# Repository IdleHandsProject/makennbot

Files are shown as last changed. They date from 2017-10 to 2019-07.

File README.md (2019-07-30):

# Make: Arduino Neural Network Robot
A light avoiding robot that navigates using a Neural Network.

# Watch the Build Series!
3 Part Series on YouTube (https://youtu.be/wtNaPLmpy1I)

BOM Here: https://www.findchips.com/org/10-open-hardware/list/53285-makennbot

HackADay.io Link: https://hackaday.io/project/27938-arduino-neural-network-robot

Motors: https://www.pololu.com/product/2357

OLED: https://www.aliexpress.com/item/White-0-66-inch-OLED-Display-Module-64x48-0-66-LCD-Screen-SPI-for-Arduino-AVR/32782787258.html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

Battery(anything with JST SH connector): https://www.sparkfun.com/products/13851

A viewer created a method to train the network using a Python Script, Check it out here: https://github.com/JonComo/Arduino_weight_trainer

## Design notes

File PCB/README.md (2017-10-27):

# Make: Arduino Neural Network Robot
A light avoiding robot that navigates using a Neural Network.

BOM Here: https://www.findchips.com/org/10-open-hardware/list/53285-makennbot

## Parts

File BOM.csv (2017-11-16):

ref | value | footprint | Digikey Part No. | Mouser Part No. | Quantity
U4 | MCP73831T | idlehands_footprints:sot23-5 | MCP73831T-2ACI/OTCT-ND |  | 1
U5 | DRV8835 | project_footprints:WSON-12-2x3 | 296-30391-1-ND |  | 1
U3 | AP2112K-3.3V | TO_SOT_Packages_SMD:SOT-23-5 | AP2112K-3.3TRG1DICT-ND |  | 1
Y1 | Crystal_Small | project_footprints:crystal_smd_5x3.2mm | 535-9536-1-ND |  | 1
R18 | 33k | Resistors_SMD:R_0603 | 311-33KGRCT-ND |  | 1
P3 | CONN_01X07 | Pin_Headers:Pin_Header_Straight_1x07 | S7040-ND |  | 1
D1 | D_Schottky | idlehands_footprints:sod80c | B130-FDICT-ND |  | 1
R2 | 330 | Resistors_SMD:R_0603 | 311-330GRCT-ND |  | 1
C13 | 10uF | Capacitors_SMD:C_0603 | 587-1256-1-ND |  | 1
F1 | 500mA | project_footprints:c_1206 | 507-1803-1-ND |  | 1
R4 R5 | 47K | Resistors_SMD:R_0603 | 311-47.0KHRCT-ND |  | 2
C6 C9 | 2.2uF | Capacitors_SMD:C_0603 | 587-1430-1-ND |  | 2
C3 C5 C1 C11 C12 C14 C15 | 0.1uF | Capacitors_SMD:C_0603 | 478-1239-1-ND |  | 7
C10 C7 | 4.7uF | Capacitors_SMD:C_0603 | 490-5421-1-ND |  | 2
D6 | RX | project_footprints:Led_0603 | 160-1447-1-ND |  | 1
U1 | 74AHC1G125 | project_footprints:sot23-5 | 1727-6024-1-ND |  | 1
R1 | 100k | Resistors_SMD:R_0603 | 311-100KHRCT-ND |  | 1
D7 | TX | project_footprints:Led_0603 | 160-1448-1-ND |  | 1
P17 | DBG_CONN | Pin_Headers:Pin_Header_Straight_2x05_Pitch1.27mm | 1175-1627-ND |  | 1
P4 P5 | MOTOR_A | Capacitors_SMD:C_1206 | F3781-ND |  | 2
PH4 PH3 PH2 PH1 | Photores | Pin_Headers:Pin_Header_Straight_1x02 | PDV-P8001-ND |  | 4
Q1 | Q_PMOS_DSG | project_footprints:SOT23 | DMG2307L-7DICT-ND |  | 1
C2 C4 | 15pF | Capacitors_SMD:C_0603 | 1276-2192-1-ND |  | 2
Q2 | Q_PMOS_GSD | idlehands_footprints:SOT23 | IRLML6402PBFCT-ND |  | 1
U2 | SAMD21G18 | project_footprints:TQFP-48_7x7mm_Pitch0.5mm | ATSAMD21G18A-AU-ND |  | 1
P1 | USB_OTG | Connect:USB_Micro-B | 609-4618-1-ND |  | 1
P2 | BatteryHolder | Connectors_JST_PH:Connectors_JST_S2B-PH-K | 36-2479-ND |  | 1
R14 R13 R19 | 1k | Resistors_SMD:R_0603 | 311-1.0KGRCT-ND |  | 3
SW2 SW3 SW4 | SW_PUSH | Buttons_Switches_SMD:SW_SPST_EVQPE1 | 401-1702-1-ND |  | 3
L1 | FB - 30Ohm | project_footprints:R_SM0603 | 445-2986-1-ND |  | 1
R3 R6 R9 R11 R15 | 10k | Resistors_SMD:R_0603 | 311-10KGRCT-ND |  | 5
C8 | 1uF | Capacitors_SMD:C_0603 | 1276-1946-1-ND |  | 1

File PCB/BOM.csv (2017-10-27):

ref | value | footprint | Digikey Part No. | Mouser Part No. | Quantity
C14 C15 | 0.1uF | Capacitors_SMD:C_0603 | 490-6328-1-ND |  | 2
C3 C5 C1 C11 C12 | 0.1uF | Capacitors_SMD:C_0603 | 311-1343-1-ND |  | 5
U4 | MCP73831T | idlehands_footprints:sot23-5 | MCP73831T-2ACI/OTCT-ND |  | 1
U5 | DRV8835 | project_footprints:WSON-12-2x3 | 296-30391-1-ND |  | 1
U3 | AP2112K-3.3V | TO_SOT_Packages_SMD:SOT-23-5 | AP2112K-3.3TRG1DICT-ND |  | 1
D1 | D_Schottky | idlehands_footprints:sod80c | B130-FDICT-ND |  | 1
R3 R6 R9 R11 R15 | 10k | Resistors_SMD:R_0603 | 311-10KJRCT-ND |  | 5
F1 | 500mA | project_footprints:c_1206 | 507-1803-1-ND |  | 1
C2 C4 | 15pF | Capacitors_SMD:C_0603 | 712-1261-1-ND |  | 2
R18 | 33k | Resistors_SMD:R_0603 | 311-33KJRCT-ND |  | 1
SW2 | SW_PUSH | Buttons_Switches_SMD:SW_SPST_EVQPE1 | CKN9112CT-ND |  | 1
Y1 | Crystal_Small | project_footprints:crystal_smd_5x3.2mm | 631-1002-1-ND |  | 1
SW3 | SW_PUSH | Buttons_Switches_SMD:SW_SPST_EVQPE1 | CKN9084CT-ND |  | 1
D6 | RX | project_footprints:Led_0603 | 160-1447-1-ND |  | 1
R2 | 330 | Resistors_SMD:R_0603 | 311-330JRCT-ND |  | 1
C13 | 10uF | Capacitors_SMD:C_0603 | 311-1729-1-ND |  | 1
U1 | 74AHC1G125 | project_footprints:sot23-5 | 1727-6024-1-ND |  | 1
P1 | USB_OTG | Connect:USB_Micro-B | 609-4618-1-ND |  | 1
C9 | 2.2uF | Capacitors_SMD:C_0603 | 490-10451-1-ND |  | 1
R1 | 100k | Resistors_SMD:R_0603 | 311-100KLRCT-ND |  | 1
D7 | TX | project_footprints:Led_0603 | 160-1448-1-ND |  | 1
P17 | DBG_CONN | Pin_Headers:Pin_Header_Straight_2x05_Pitch1.27mm | 1175-1627-ND |  | 1
P4 P5 | MOTOR_A | Capacitors_SMD:C_1206 | F3781-ND |  | 2
C10 C7 | 4.7uF | Capacitors_SMD:C_0603 | 490-5915-1-ND |  | 2
PH4 PH3 PH2 PH1 | Photores | Pin_Headers:Pin_Header_Straight_1x02 | PDV-P8001-ND |  | 4
Q1 | Q_PMOS_DSG | project_footprints:SOT23 | DMG2307L-7DICT-ND |  | 1
C6 | 2.2uF | Capacitors_SMD:C_0603 | 1276-1291-1-ND |  | 1
R4 R5 | 47K | Resistors_SMD:R_0603 | 311-47.0KLRCT-ND |  | 2
R14 R13 R19 | 1k | Resistors_SMD:R_0603 | 311-1.0KJRCT-ND |  | 3
Q2 | Q_PMOS_GSD | idlehands_footprints:SOT23 | IRLML6402PBFCT-ND |  | 1
U2 | SAMD21G18 | project_footprints:TQFP-48_7x7mm_Pitch0.5mm | ATSAMD21G18A-AU-ND |  | 1
C8 | 1uF | Capacitors_SMD:C_0603 | 490-1320-1-ND |  | 1
P2 | BatteryHolder | Connectors_JST_PH:Connectors_JST_S2B-PH-K | 36-2479-ND |  | 1
SW4 | SW_PUSH | Buttons_Switches_SMD:SW_SPST_EVQPE1 | 401-1702-1-ND |  | 1
L1 | FB - 30Ohm | project_footprints:R_SM0603 | 445-2986-1-ND |  | 1

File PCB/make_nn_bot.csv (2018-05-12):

Id | Designator | Package | Quantity | Designation | Supplier and ref
1 | MOTORB,MOTORA | Motor_PlasticGear_Holder | 2 | Motor_PlasticGear_Holder
2 | C1,C3,C5,C11,C12,C14,C15 | C_0603 | 7 | 0.1uF
3 | C2,C4 | C_0603 | 2 | 15pF
4 | C6,C9 | C_0603 | 2 | 2.2uF
5 | C7,C10 | C_0603 | 2 | 4.7uF
6 | C8 | C_0603 | 1 | 1uF
7 | C13 | C_0603 | 1 | 10uF
8 | D3 | LED-0603 | 1 | LED
9 | D6 | Led_0603 | 1 | RX
10 | D7 | Led_0603 | 1 | TX
11 | F1 | c_1206 | 1 | 500mA
12 | L1 | R_SM0603 | 1 | FB - 30Ohm
13 | P1 | USB_Micro-B | 1 | USB_OTG
14 | P3 | Pin_Header_Straight_1x07 | 1 | CONN_01X07
15 | P4 | C_1206 | 1 | MOTOR_A
16 | P5 | C_1206 | 1 | MOTOR_B
17 | Q2 | SOT23 | 1 | Q_PMOS_GSD
18 | R1 | R_0603 | 1 | 100k
19 | R2 | R_0603 | 1 | 330
20 | R3 | R_0603 | 1 | 10k
21 | R4,R5 | R_0603 | 2 | 47K
22 | R6,R9,R11,R15 | R_0603 | 4 | 10K
23 | PH1,PH2,PH3,PH4 | Pin_Header_Straight_1x02 | 4 | Photores
24 | R13,R14 | R_0603 | 2 | 1k
25 | R19 | R_0603 | 1 | 1K
26 | RIGHT,LEFT,RESET | SW_SPST_EVQPE1 | 3 | SW_PUSH
27 | U1 | sot23-5 | 1 | 74AHC1G125
28 | U2 | TQFP-48_7x7mm_Pitch0.5mm | 1 | SAMD21G18
29 | U3 | SOT-23-5 | 1 | AP2112K-3.3V
30 | U4 | sot23-5 | 1 | MCP73831T
31 | U5 | WSON-12-2x3 | 1 | DRV8835
32 | REF** | Wheel_Ball | 1 | Wheel_Ball
33 | Y1 | crystal_smd_3.2x1.5 | 1 | Crystal_Small
34 | D1 | bat20j | 1 | D_Schottky
35 | PWR1 | Pin_Header_Straight_1x03 | 1 | SWITCH_INV
36 | R18 | R_0603 | 1 | 33k
37 | P2 | Connectors_JST_S2B-PH-K | 1 | BatteryHolder
38 | G***,G*** | Make_Logo | 2 | LOGO
39 | G*** | IdlehandsdevLogo | 1 | LOGO
40 | G*** | OSHLogo | 1 | LOGO
41 | P17 | Atmel_ICE_Connector_02x05 | 1 | DBG_CONN
42 | Q1 | DMG2307L_SOT23 | 1 | Q_PMOS_DSG

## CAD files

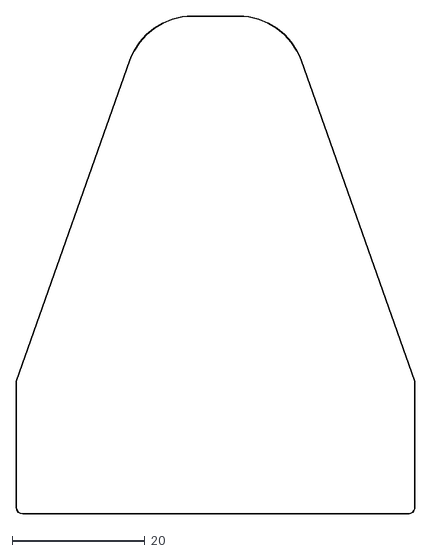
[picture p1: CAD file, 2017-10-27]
CAD/PCB_outline.dxf
60.0 x 75.0

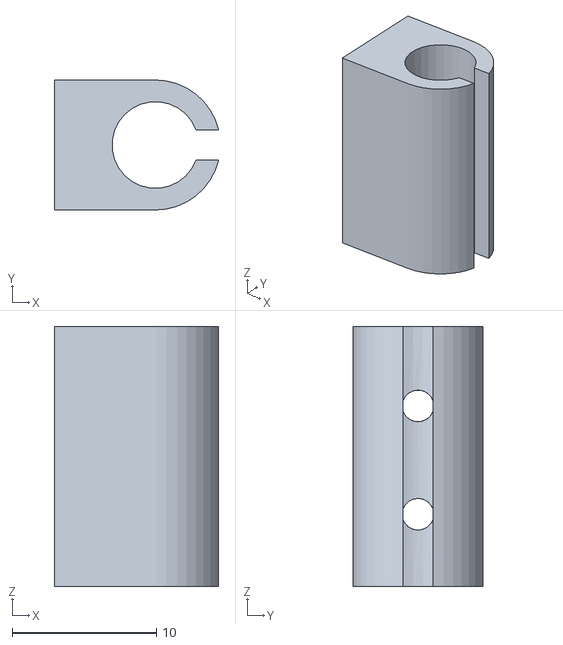
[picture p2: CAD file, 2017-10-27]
CAD/MotorMount.stl
11.4 x 9.00 x 18.0

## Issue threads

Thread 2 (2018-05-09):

Wheels & Casters

profshanks, 2018-05-09:
Where did you source the wheels that go on the motor and the little ball-caster?

Apologies if I missed this in the other documentation posted here.

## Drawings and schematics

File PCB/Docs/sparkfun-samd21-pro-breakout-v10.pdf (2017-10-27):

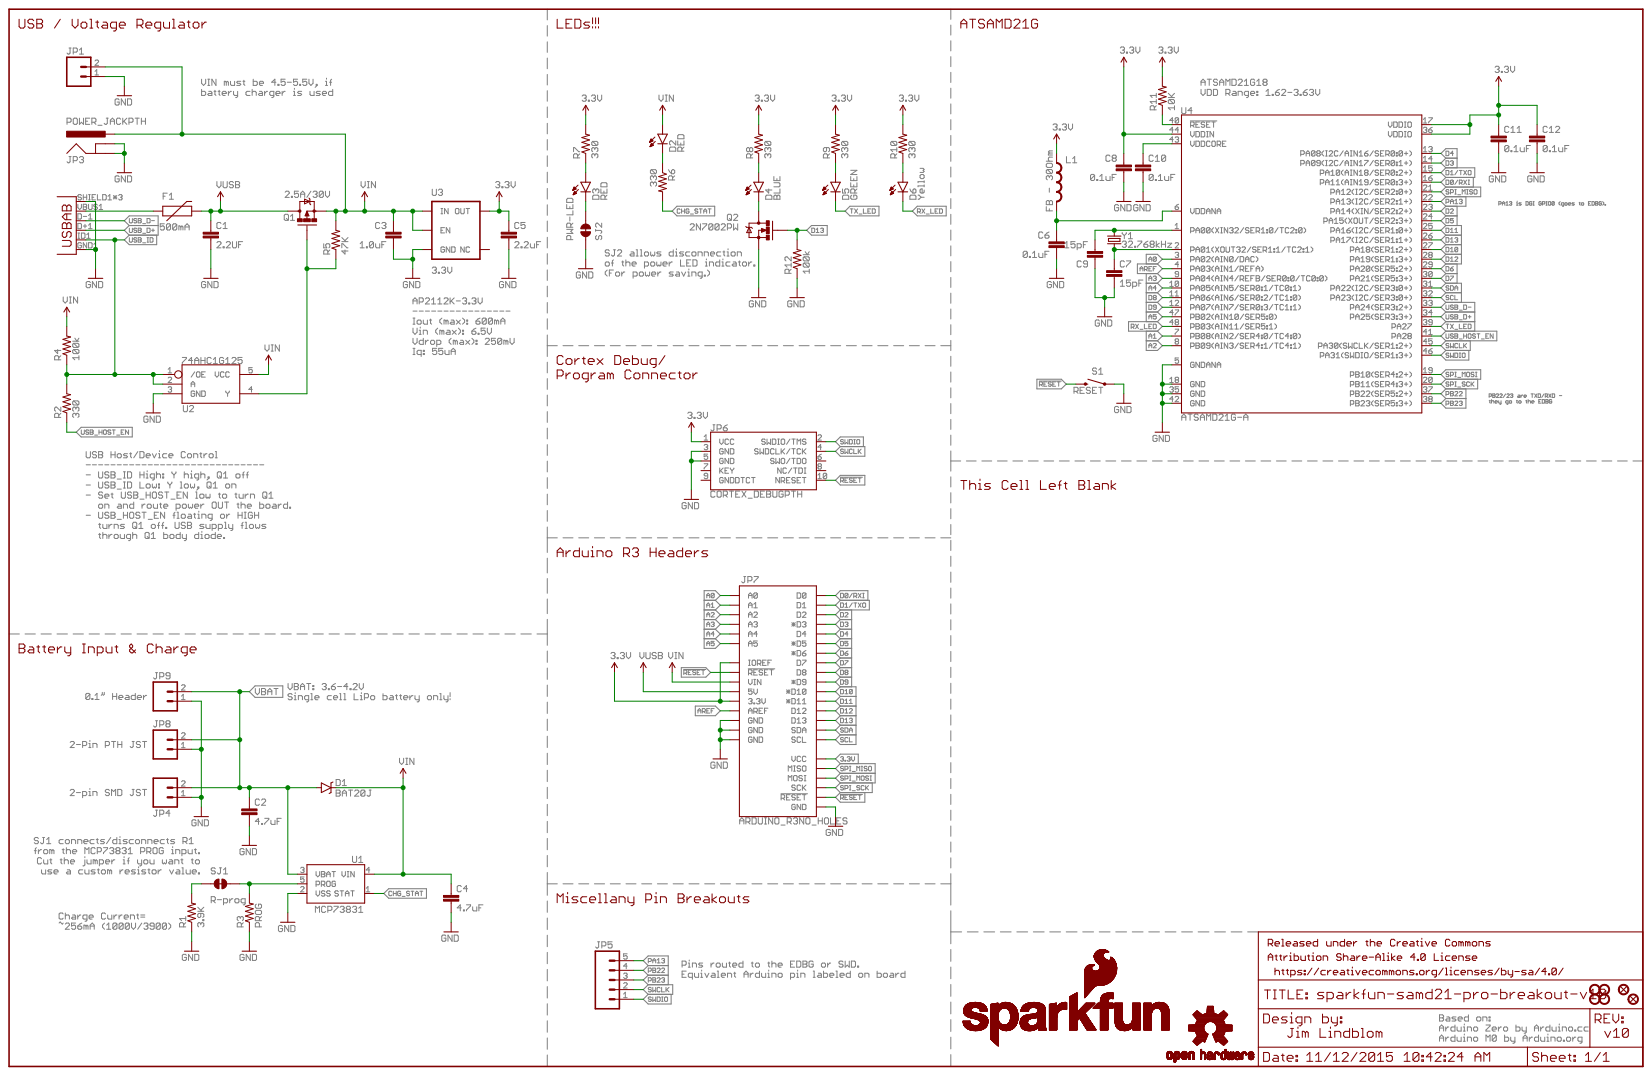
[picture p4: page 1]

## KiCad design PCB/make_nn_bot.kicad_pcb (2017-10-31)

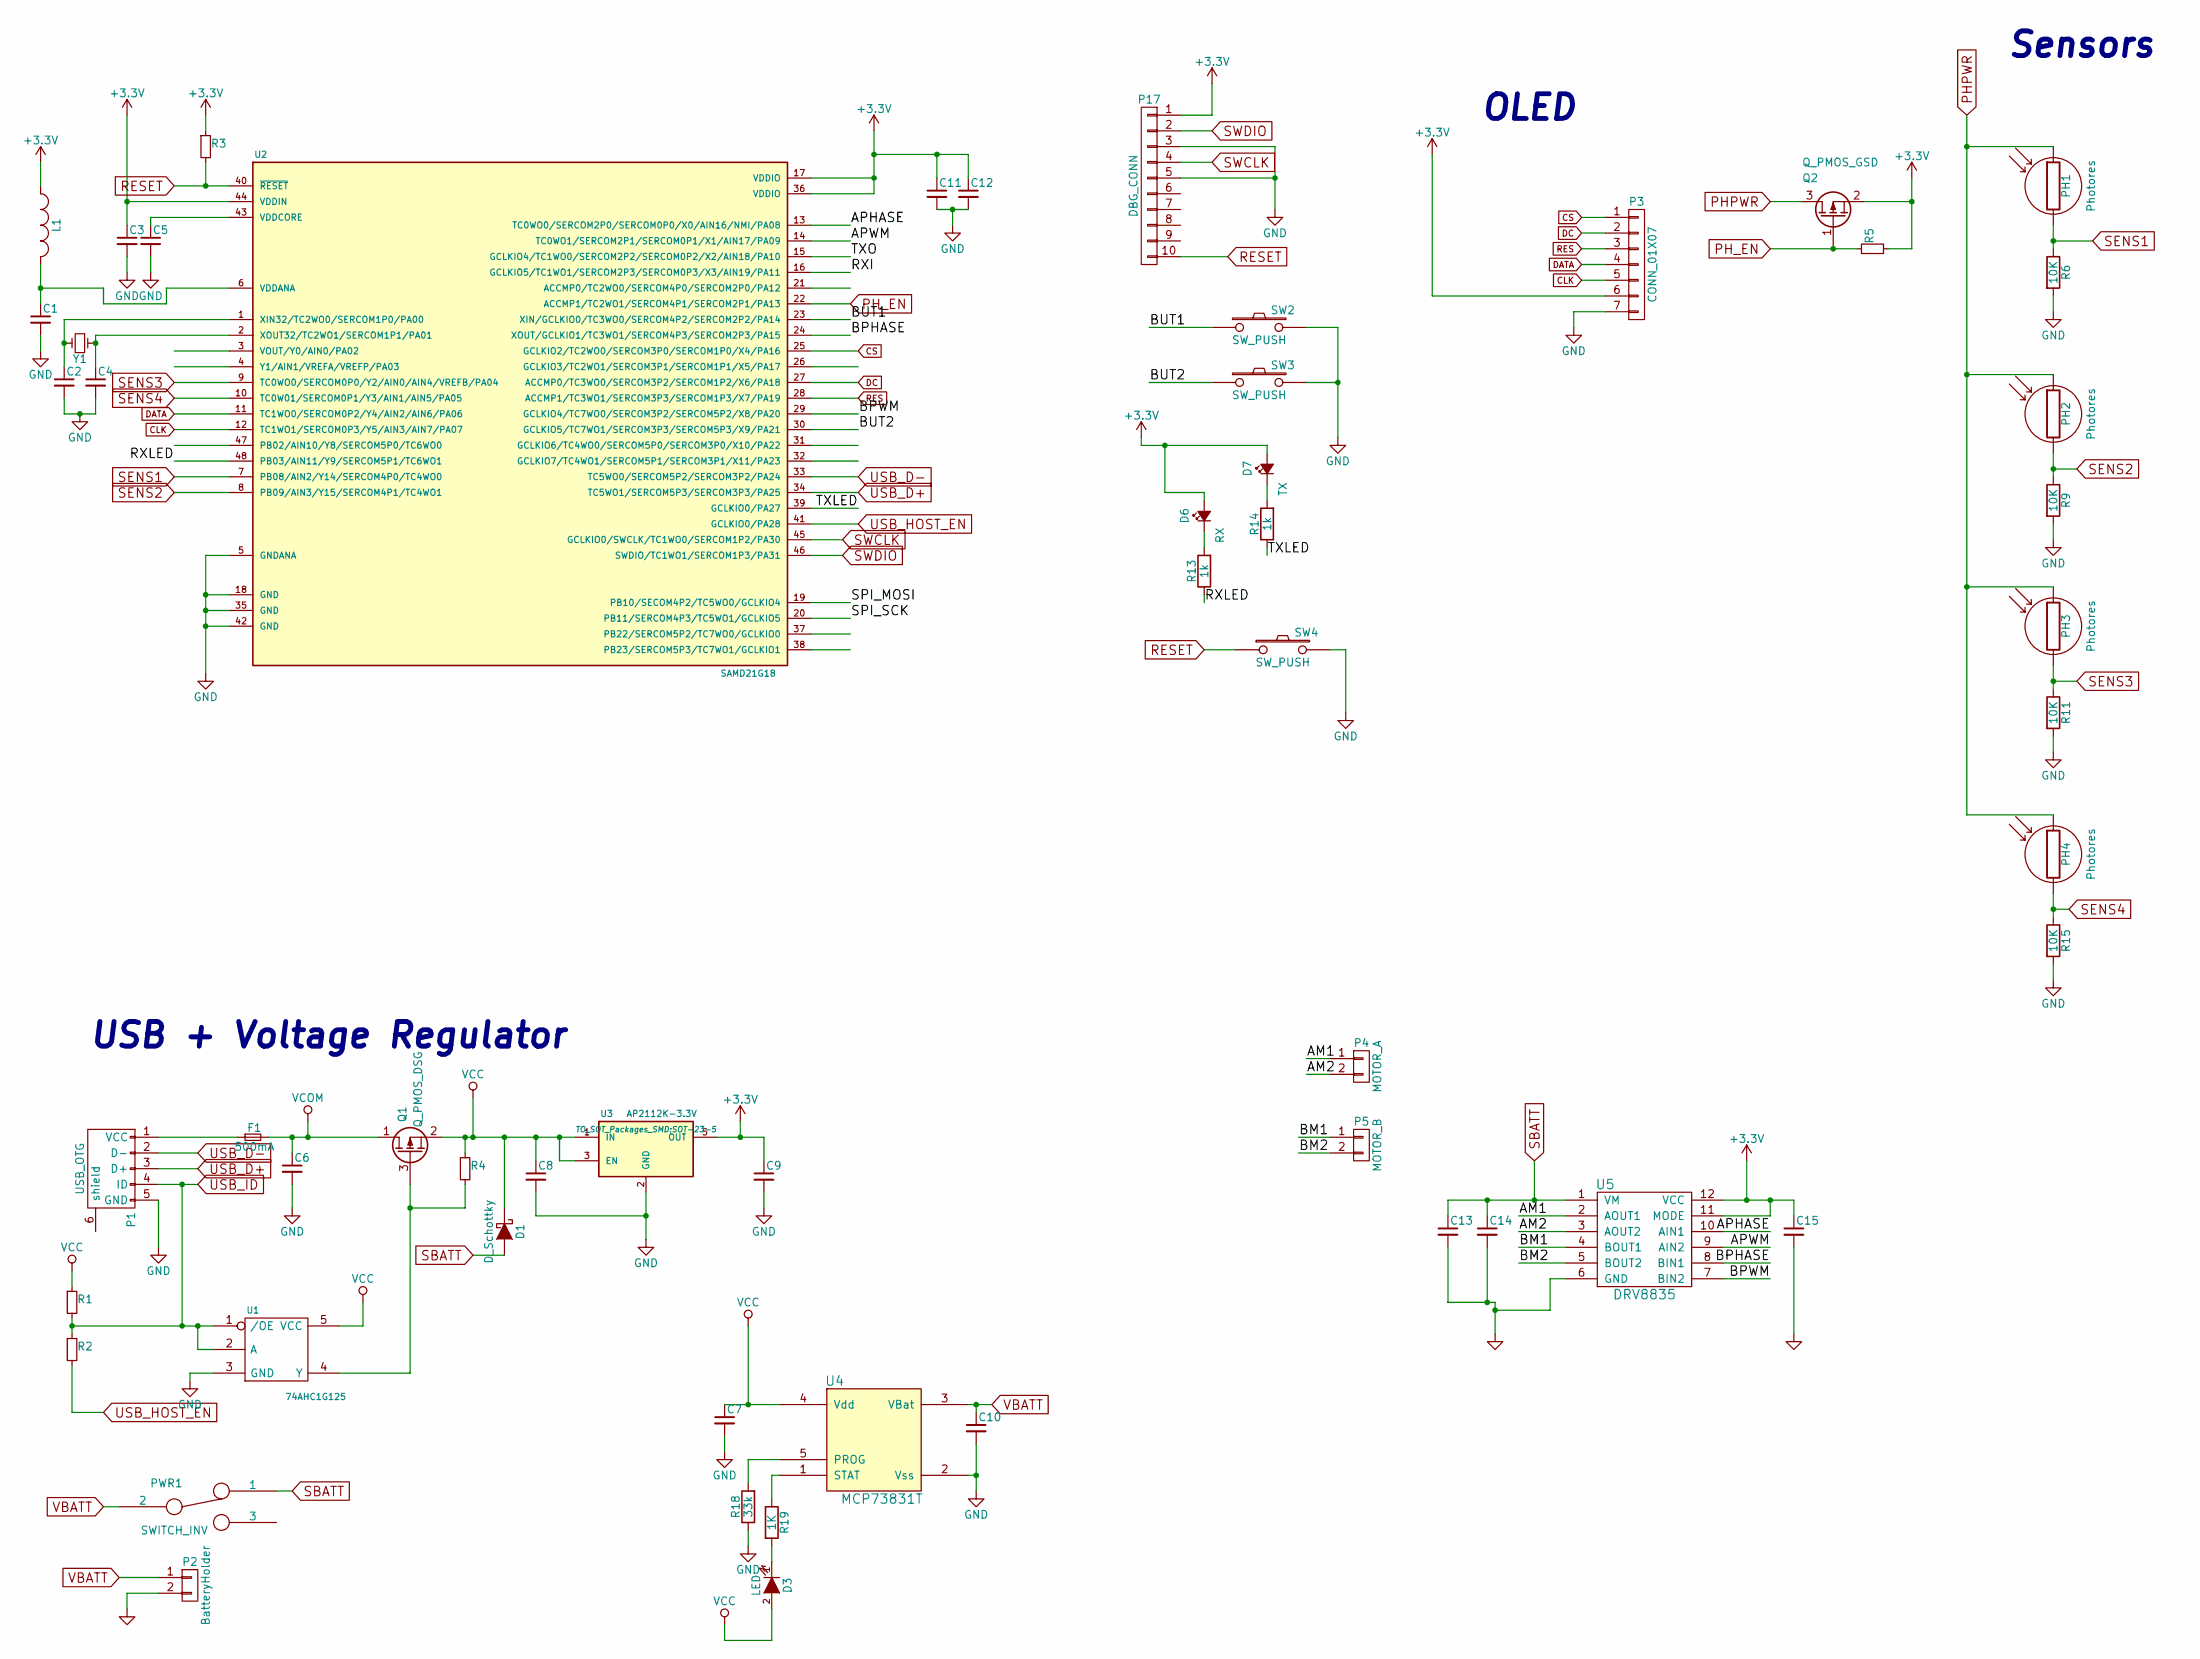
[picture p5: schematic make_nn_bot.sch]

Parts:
C1, C3, C5, C11, C12: 0.1uF; C_0603; Digikey Part No. 311-1343-1-ND
C2, C4: 15pF; C_0603; Digikey Part No. 712-1261-1-ND
C6: 2.2uF; C_0603; Digikey Part No. 1276-1291-1-ND
C7, C10: 4.7uF; C_0603; Digikey Part No. 490-5915-1-ND
C8: 1uF; C_0603; Digikey Part No. 490-1320-1-ND
C9: 2.2uF; C_0603; Digikey Part No. 490-10451-1-ND
C13: 10uF; C_0603; Digikey Part No. 311-1729-1-ND
C14, C15: 0.1uF; C_0603; Digikey Part No. 490-6328-1-ND
D1: D_Schottky; sod80c; Digikey Part No. B130-FDICT-ND
D3: LED; LED-0603
D6: RX; Led_0603; Digikey Part No. 160-1447-1-ND
D7: TX; Led_0603; Digikey Part No. 160-1448-1-ND
F1: 500mA; c_1206; Digikey Part No. 507-1803-1-ND
L1: FB - 30Ohm; R_SM0603; Digikey Part No. 445-2986-1-ND
P1: USB_OTG; USB_Micro-B; Digikey Part No. 609-4618-1-ND
P2: BatteryHolder; Connectors_JST_S2B-PH-K; Digikey Part No. 36-2479-ND
P3: CONN_01X07; Pin_Header_Straight_1x07
P4: MOTOR_A; C_1206; Digikey Part No. F3781-ND
P5: MOTOR_B; C_1206; Digikey Part No. F3781-ND
P17: DBG_CONN; Pin_Header_Straight_2x05_Pitch1.27mm; Digikey Part No. 1175-1627-ND
PH1, PH2, PH3, PH4: Photores; Pin_Header_Straight_1x02; Digikey Part No. PDV-P8001-ND
PWR1: SWITCH_INV; Pin_Header_Straight_1x03
Q1: Q_PMOS_DSG; SOT23; Digikey Part No. DMG2307L-7DICT-ND
Q2: Q_PMOS_GSD; SOT23; Digikey Part No. IRLML6402PBFCT-ND
R1: 100k; R_0603; Digikey Part No. 311-100KLRCT-ND
R2: 330; R_0603; Digikey Part No. 311-330JRCT-ND
R3: 10k; R_0603; Digikey Part No. 311-10KJRCT-ND
R4, R5: 47K; R_0603; Digikey Part No. 311-47.0KLRCT-ND
R6, R9, R11, R15: 10K; R_0603; Digikey Part No. 311-10KJRCT-ND
R13, R14: 1k; R_0603; Digikey Part No. 311-1.0KJRCT-ND
R18: 33k; R_0603; Digikey Part No. 311-33KJRCT-ND
R19: 1K; R_0603; Digikey Part No. 311-1.0KJRCT-ND
SW2: SW_PUSH; SW_SPST_EVQPE1; Digikey Part No. CKN9112CT-ND
SW3: SW_PUSH; SW_SPST_EVQPE1; Digikey Part No. CKN9084CT-ND
SW4: SW_PUSH; SW_SPST_EVQPE1; Digikey Part No. 401-1702-1-ND
U1: 74AHC1G125; sot23-5; Digikey Part No. 1727-6024-1-ND
U2: SAMD21G18; TQFP-48_7x7mm_Pitch0.5mm; Digikey Part No. ATSAMD21G18A-AU-ND
U3: AP2112K-3.3V; SOT-23-5; Digikey Part No. AP2112K-3.3TRG1DICT-ND
U4: MCP73831T; sot23-5; Digikey Part No. MCP73831T-2ACI/OTCT-ND
U5: DRV8835; WSON-12-2x3; Digikey Part No. 296-30391-1-ND
Y1: Crystal_Small; crystal_smd_5x3.2mm; Digikey Part No. 631-1002-1-ND

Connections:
+3V3: C3.1, C9.1, C11.1, C12.1, C15.1, D6.2 (A), D7.2 (A), L1.1, P3.6, P17.1, Q2.2 (S), R3.1, R5.2, U2.17 (VDDIO), U2.36 (VDDIO), U2.44 (VDDIN), U3.5 (OUT), U5.11 (MODE), U5.12 (VCC)
/AM1: P4.1, U5.2 (AOUT1)
/AM2: P4.2, U5.3 (AOUT2)
/APHASE: U2.13 (TC0WO0/SERCOM2P0/SERCOM0P0/X0/AIN16/NMI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), U5.10 (AIN1)
/APWM: U2.14 (TC0WO1/SERCOM2P1/SERCOM0P1/X1/AIN17/PA09), U5.9 (AIN2)
/BM1: P5.1, U5.4 (BOUT1)
/BM2: P5.2, U5.5 (BOUT2)
/BPHASE: U2.24 (XOUT/GCLKIO1/TC3WO1/SERCOM4P3/SERCOM2P3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), U5.8 (BIN1)
/BPWM: U2.29 (GCLKIO4/TC7WO0/SERCOM3P2/SERCOM5P2/X8/P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), U5.7 (BIN2)
/BUT1: SW2.1, U2.23 (XIN/GCLKIO0/TC3WO0/SERCOM4P2/SERCOM2P2/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); also elsewhere on the board
/BUT2: SW3.1, U2.30 (GCLKIO5/TC7WO1/SERCOM3P3/SERCOM5P3/X9/P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); also elsewhere on the board
/RXI: U2.16 (GCLKIO5/TC1WO1/SERCOM2P3/SERCOM0P3/X3/A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)
/RXLED: R13.1, U2.48 (PB03/AIN11/Y9/SERCOM5P1/TC6WO1)
/SPI_MOSI: U2.19 (PB10/SECOM4P2/TC5WO0/GCLKIO4)
/SPI_SCK: U2.20 (PB11/SERCOM4P3/TC5WO1/GCLKIO5)
/TXLED: R14.1, U2.39 (GCLKIO0/PA27)
/TXO: U2.15 (GCLKIO4/TC1WO0/SERCOM2P2/SERCOM0P2/X2/A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)
CLK: P3.5, U2.12 (TC1WO1/SERCOM0P3/Y5/AIN3/AIN7/PA07)
CS: P3.1, U2.25 (GCLKIO2/TC2WO0/SERCOM3P0/SERCOM1P0/X4/P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)
DATA: P3.4, U2.11 (TC1WO0/SERCOM0P2/Y4/AIN2/AIN6/PA06)
DC: P3.2, U2.27 (ACCMP0/TC3WO0/SERCOM3P2/SERCOM1P2/X6/PA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)
GND: C1.2, C2.2, C3.2, C4.2, C5.2, C6.2, C7.2, C8.2, C9.2, C10.2, C11.2, C12.2, C13.2, C14.2, C15.2, P1.5 (GND), P2.2, P3.7, P17.3, P17.5, R6.2, R9.2, R11.2, R15.2, R18.1, SW2.2, SW3.2, SW4.2, U1.3 (GND), U2.5 (GNDANA), U2.18 (GND), U2.35 (GND), U2.42 (GND), U3.2 (GND), U4.2 (Vss), U5.6 (GND); also elsewhere on the board
unnamed: C1.1, L1.2, U2.6 (VDDANA)
unnamed: C2.1, U2.1 (XIN32/TC2WO0/SERCOM1P0/PA00), Y1.2
unnamed: C4.1, U2.2 (XOUT32/TC2WO1/SERCOM1P1/PA01), Y1.1
unnamed: C5.1, U2.43 (VDDCORE)
unnamed: D3.1 (K), R19.2
unnamed: D6.1 (K), R13.2
unnamed: D7.1 (K), R14.2
unnamed: F1.1, P1.1 (VCC)
unnamed: Q1.3 (G), R4.2, U1.4 (Y)
unnamed: R18.2, U4.5 (PROG)
unnamed: R19.1, U4.1 (STAT)
PHPWR: PH1.1, PH2.1, PH3.1, PH4.1, Q2.3 (D)
PH_EN: Q2.1 (G), R5.1, U2.22 (ACCMP1/TC2WO1/SERCOM4P1/SERCOM2P1/PA13)
RES: P3.3, U2.28 (ACCMP1/TC3WO1/SERCOM3P3/SERCOM1P3/X7/PA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)
RESET: P17.10, R3.2, SW4.1, U2.40 (~RESET~); also elsewhere on the board
SBATT: C13.1, C14.1, D1.2 (A), PWR1.1, U5.1 (VM)
SENS1: PH1.2, R6.1, U2.7 (PB08/AIN2/Y14/SERCOM4P0/TC4WO0)
SENS2: PH2.2, R9.1, U2.8 (PB09/AIN3/Y15/SERCOM4P1/TC4WO1)
SENS3: PH3.2, R11.1, U2.9 (TC0WO0/SERCOM0P0/Y2/AIN0/AIN4/VREFB/PA04)
SENS4: PH4.2, R15.1, U2.10 (TC0W01/SERCOM0P1/Y3/AIN1/AIN5/PA05)
SWCLK: P17.4, U2.45 (GCLKIO0/SWCLK/TC1WO0/SERCOM1P2/PA30)
SWDIO: P17.2, U2.46 (SWDIO/TC1WO1/SERCOM1P3/PA31)
USB_D+: P1.3 (D+), U2.34 (TC5WO1/SERCOM5P3/SERCOM3P3/PA25)
USB_D-: P1.2 (D-), U2.33 (TC5WO0/SERCOM5P2/SERCOM3P2/PA24)
USB_HOST_EN: R2.2, U2.41 (GCLKIO0/PA28)
USB_ID: P1.4 (ID), R1.2, R2.1, U1.1 (/OE), U1.2 (A)
VBATT: C10.1, P2.1, PWR1.2, U4.3 (VBat)
VCC: C7.1, C8.1, D1.1 (K), D3.2 (A), Q1.2 (S), R1.1, R4.1, U1.5 (VCC), U3.1 (IN), U3.3 (EN), U4.4 (Vdd)
VCOM: C6.1, F1.2, Q1.1 (D)

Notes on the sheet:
USB + Voltage Regulator
Sensors
OLED

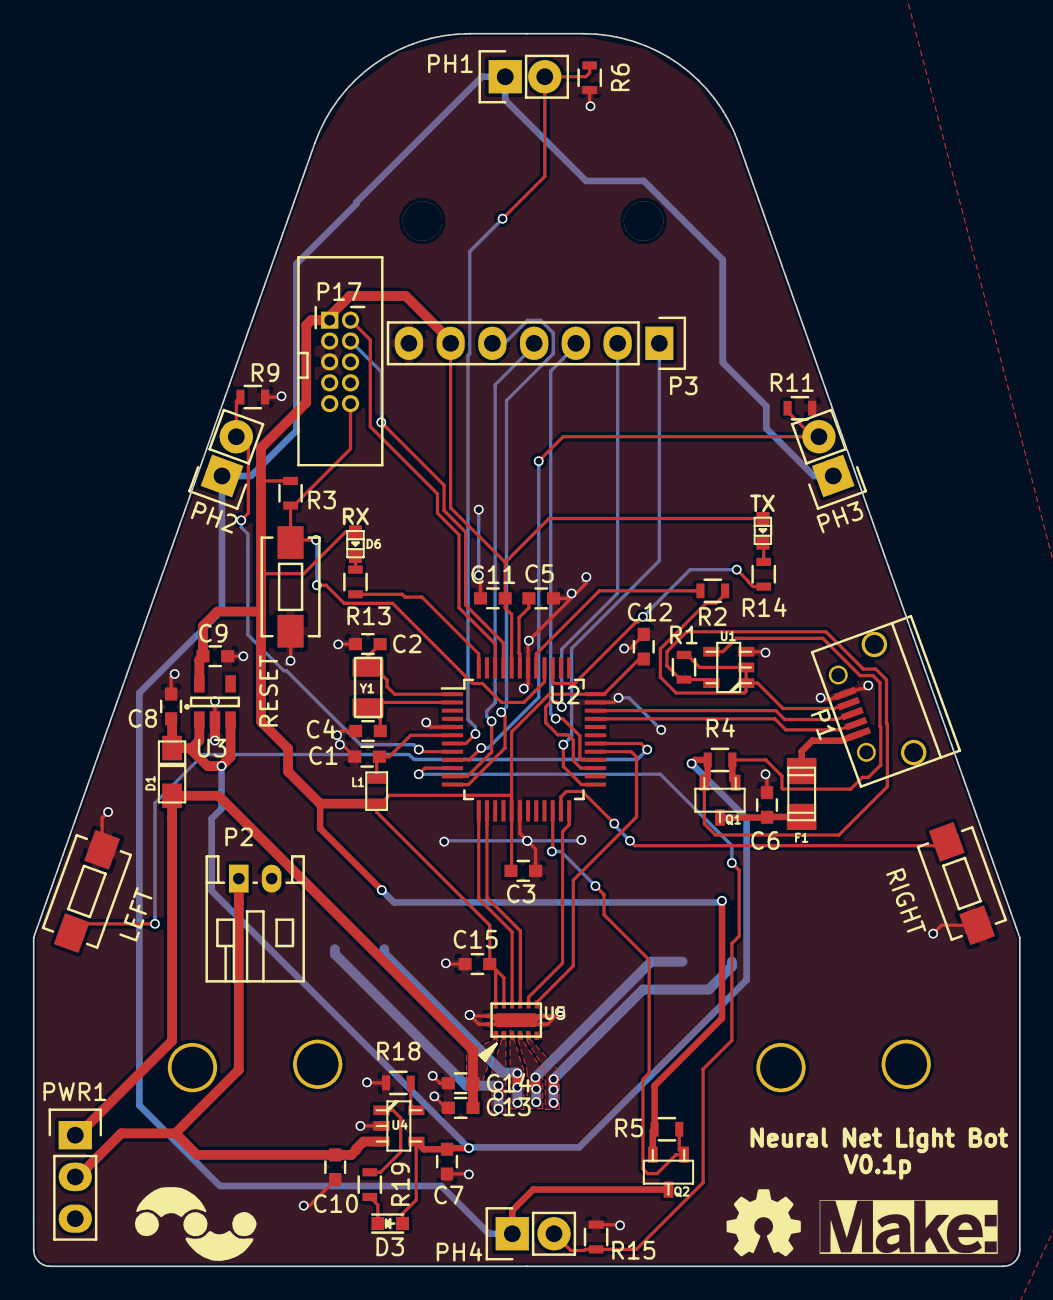
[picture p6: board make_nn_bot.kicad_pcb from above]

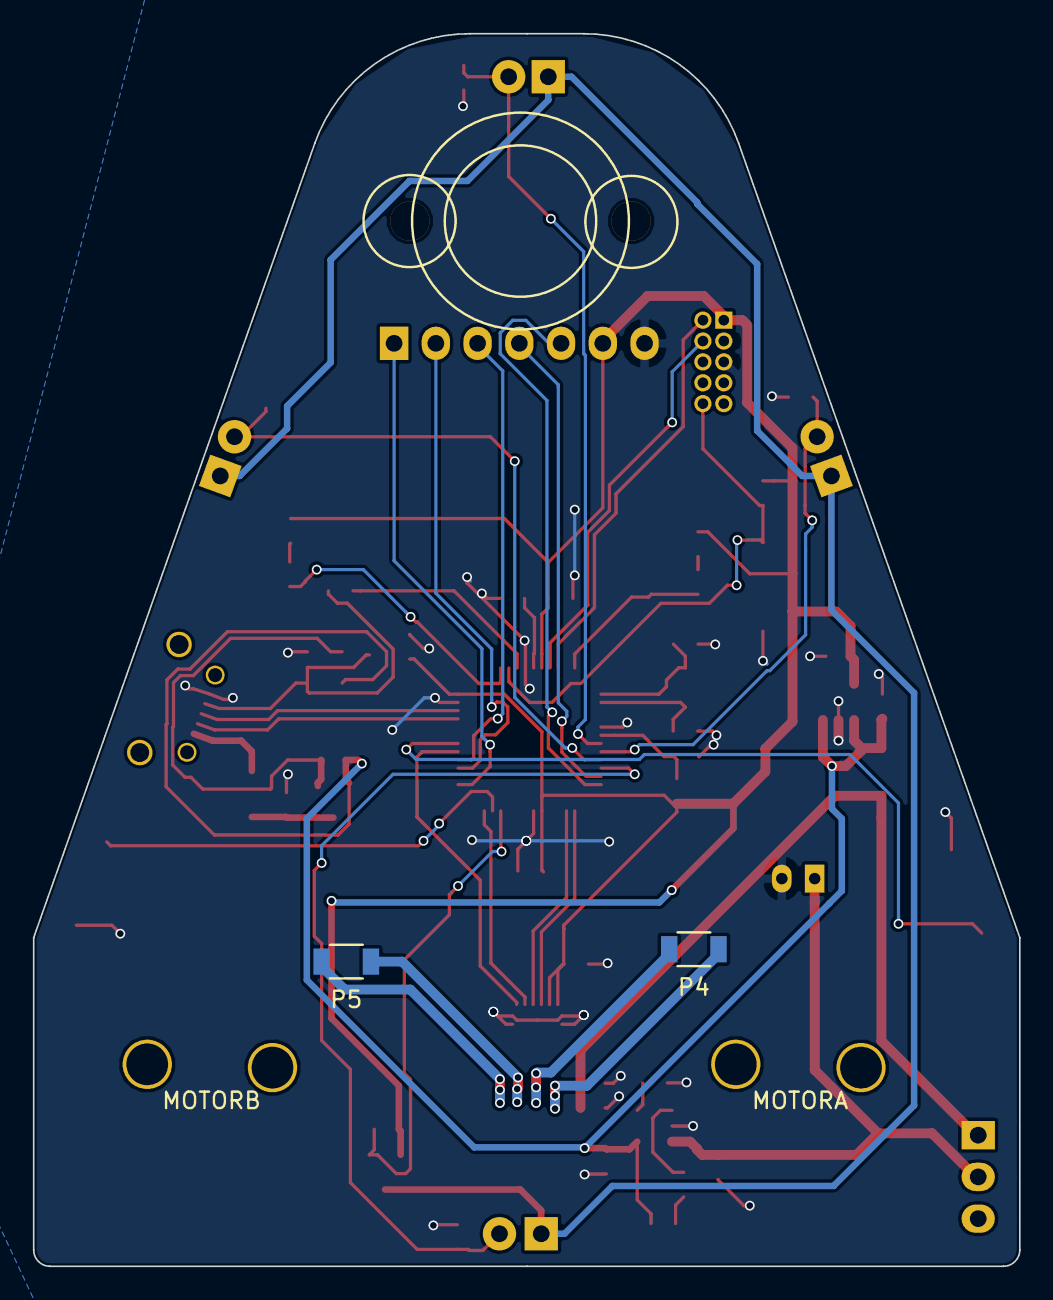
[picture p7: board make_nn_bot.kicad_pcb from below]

Board: 2 copper layers, 60.0 x 75.0 mm, 58 parts (4 on the bottom side), 47 nets.

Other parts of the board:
LEFT: SW_PUSH; SW_SPST_EVQPE1
MOTORA: Motor_PlasticGear_Holder
MOTORB: Motor_PlasticGear_Holder
RESET: SW_PUSH; SW_SPST_EVQPE1
RIGHT: SW_PUSH; SW_SPST_EVQPE1

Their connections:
/BUT1: RIGHT.1; also elsewhere on the board
/BUT2: LEFT.1; also elsewhere on the board
GND: LEFT.2, RESET.2, RIGHT.2; also elsewhere on the board
RESET: RESET.1; also elsewhere on the board

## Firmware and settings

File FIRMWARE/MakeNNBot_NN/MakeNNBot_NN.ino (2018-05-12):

/************************************************
   Make: Arduino Neural Network Robot
   01/11/2017
   This firmware is comprised of various open source libraries and examples.
   Original elements created by Sean Hodgins
   This firmware is free and open source and can be found here: https://github.com/idlehandsproject/makennbot

   Information on the Neural Network and the code
   can be found here: http://robotics.hobbizine.com/arduinoann.html

   For the OLED screen, the U8G2 library can be found here: https://github.com/olikraus/u8g2

*/

#include <Arduino.h>
#include <U8g2lib.h>
#include "make_logo.h"

#include <math.h>
#define DEBUG

#ifdef U8X8_HAVE_HW_SPI
#include <SPI.h>
#endif
#ifdef U8X8_HAVE_HW_I2C
#include <Wire.h>
#endif

U8G2_SSD1306_64X48_ER_F_4W_SW_SPI u8g2(U8G2_R0, 9, 8, 11, 10, 12);

int PH1, PH2, PH3, PH4;
int PHEN = 38;
int menu = 1;
int curr_menu = 1;
int prog_start = 0;
int menu_items = 3;

#define APHASE 4
#define APWM 3
#define BPHASE 5
#define BPWM 6
#define left_b 7
#define right_b 2

#define LEDYEL 25
#define LEDRED 26

/******************************************************************
   Network Configuration - customized per network
 ******************************************************************/

const int PatternCount = 16;
const int InputNodes = 4;
const int HiddenNodes = 5;
const int OutputNodes = 2;
const float LearningRate = 0.3;
const float Momentum = 0.9;
const float InitialWeightMax = 0.5;
const float Success = 0.0015;

float Input[PatternCount][InputNodes] = {
  { 0, 1, 1, 0 },  // LIGHT ON LEFT AND RIGHT
  { 0, 1, 0, 0 },  // LIGHT ON LEFT
  { 1, 1, 1, 0 },  // LIGHT ON TOP, LEFT, and RIGHT
  { 1, 1, 0, 0 },  // LIGHT ON TOP and LEFT
  { 0, 0, 1, 0 },  // LIGHT ON RIGHT
  { 1, 0, 0, 0 },  // LIGHT ON TOP
  { 0, 0, 0, 0 },  // NO LIGHT
  { 0, 0, 0, 1 },  // LIGHT ON BOTTOM
  { 0, 1, 0, 1 },  // LIGHT ON BOTTOM AND LEFT
  { 0, 0, 1, 1 },  // LIGHT ON BOTTOM AND RIGHT
  { 0, 1, 1, 1 },  // LIGHT ON BOTTOM, LEFT, and RIGHT
  { 1, 0, 0, 1 },  // LIGHT ON TOP AND BOTTOM
  { 1, 1, 0, 1 },  // LIGHT ON TOP, BOTTOM, and LEFT
  { 1, 0, 1, 1 },  // LIGHT ON TOP, BOTTOM, and RIGHT
  { 1, 0, 1, 0 },  // LIGHT ON TOP AND RIGHT
  { 1, 1, 1, 1 },  // LIGHT ON ALL

};

const float Target[PatternCount][OutputNodes] = {
  { 0.65, 0.55 },   //LEFT MOTOR SLOW
  { 0.75, 0.5 },    //LEFT MOTOR FASTER
  { 0.2, 0.2 },     //BOTH MOTORS FULL BACKWARDS
  { 1, 0.2 },       //MOTOR LEFT FULL FORWARD, RIGHT BACKWARDS
  { 0.5, 0.75 },    //MOTOR LEFT STOPPED, RIGHT FORWARDS
  { 0.3, 0.3 },     //BOTH BACKWARDS
  { 0.5, 0.5 },     //BOTH MOTORS STOPPED
  { 0.75, 0.75 },
  { 1, 0.75 },
  { 0.75, 1 },
  { 1, 1 },
  { 1, 0 },
  { 1, 0.75 },
  { 0.75, 1 },
  { 0.2, 1 },
  { 0.65, 0.65},
};

/******************************************************************
   End Network Configuration
 ******************************************************************/

int i, j, p, q, r;
int ReportEvery1000;
int RandomizedIndex[PatternCount];
long  TrainingCycle;
float Rando;
float Error = 2;
float Accum;

float Hidden[HiddenNodes];
float Output[OutputNodes];

float HiddenWeights[InputNodes + 1][HiddenNodes];
float OutputWeights[HiddenNodes + 1][OutputNodes];
float HiddenDelta[HiddenNodes];
float OutputDelta[OutputNodes];
float ChangeHiddenWeights[InputNodes + 1][HiddenNodes];
float ChangeOutputWeights[HiddenNodes + 1][OutputNodes];

int ErrorGraph[64];

void setup() {
  // put your setup code here, to run once:
  for (int x = 0; x < 64; x++) {
    ErrorGraph[x] = 47;
  }

  pinMode(A1, INPUT);
  pinMode(A2, INPUT);
  pinMode(A3, INPUT);
  pinMode(A4, INPUT);
  pinMode(left_b, INPUT_PULLUP);
  pinMode(right_b, INPUT_PULLUP);

  pinMode(PHEN, OUTPUT);
  digitalWrite(PHEN, LOW);




  randomSeed(analogRead(A1));       //Collect a random ADC sample for Randomization.
  ReportEvery1000 = 1;
  for ( p = 0 ; p < PatternCount ; p++ ) {
    RandomizedIndex[p] = p ;
  }

  SerialUSB.begin(115200);
  delay(100);
  u8g2.begin();

  u8g2.setFlipMode(0);
  u8g2.setFont(u8g2_font_6x12_tr);
  u8g2.setColorIndex(1);
  int testmode = 1;
  testmode = digitalRead(left_b);
  if (testmode == 0) {
    motorTesting();
  }

  u8g2.firstPage();
  do {
    drawLogo();
  } while ( u8g2.nextPage() );
  delay(2000);
  u8g2.firstPage();
  do {
    intro();
  } while ( u8g2.nextPage() );
  attachInterrupt(left_b, menu_change, LOW);
  attachInterrupt(right_b, load_prog, LOW);
  delay(1000);
  while (prog_start == 0) {
    u8g2.firstPage();
    do {
      menu_select();
    } while ( u8g2.nextPage() );
  }
  u8g2.clear();
  delay(1000);

}

void loop() {

  //motorTesting() //Run this to test the direction of your motors;
  while (prog_start == 0) {
    u8g2.firstPage();
    do {
      menu_select();
    } while ( u8g2.nextPage() );
  }
  u8g2.clear();
  delay(1000);
  switch (curr_menu) {
    case 1:
      simpleLightAvoid();
      break;
    case 2:
      train_nn();
      break;
    case 3:
      drive_nn();
      break;
    default:
      break;

  }
}

//THIS IS THE SIMPLE LIGHT AVOID ROUTINE(NO NEURAL NETWORK)
void simpleLightAvoid() {
  while (1) {
    PH1 = analogRead(A1); //READ PHOTORESISTORS
    PH2 = analogRead(A2);
    PH3 = analogRead(A3);
    PH4 = analogRead(A4);
    PH1 = map(PH1, 400, 1024, 0, 48);
    PH2 = map(PH2, 400, 1024, 0, 64);
    PH3 = map(PH3, 400, 1024, 0, 64);
    PH4 = map(PH4, 400, 1024, 0, 48);
    //motorTesting();
    u8g2.firstPage();
    do {
      //drawBars(PH1,PH2,PH3,PH4);
      drawBallDir(PH1, PH2, PH3, PH4);
    } while ( u8g2.nextPage() );
  }
}


//THIS ROUTINE IS FOR TESTING THE MOTORS
void motorTesting() {
  SerialUSB.println("Driving Forward");
  u8g2.firstPage();
  do {
    u8g2.drawStr( 1, 10, "Forward");
  } while ( u8g2.nextPage() );
  motorA(70);
  motorB(70);
  delay(1000);
  SerialUSB.println("Stopping");
  u8g2.firstPage();
  do {
    u8g2.drawStr( 1, 10, "Stopping");
  } while ( u8g2.nextPage() );
  motorA(50);
  motorB(50);
  delay(1000);
  SerialUSB.println("Turning");
  u8g2.firstPage();
  do {
    u8g2.drawStr( 1, 10, "Turning");
  } while ( u8g2.nextPage() );
  motorA(70);
  motorB(20);

  delay(1000);
  u8g2.firstPage();
  do {
    u8g2.drawStr( 1, 10, "Backwards");
  } while ( u8g2.nextPage() );
  motorA(30);
  motorB(30);
  delay(1000);
  u8g2.firstPage();
  do {
    u8g2.drawStr( 1, 10, "Stopped");
  } while ( u8g2.nextPage() );
  motorA(50);
  motorB(50);
  delay(1000);
  //while (1);
}

//DRAWS THE MAKE LOGO
void drawLogo(void)
{
  uint8_t mdy = 0;
  if ( u8g2.getDisplayHeight() < 59 )
    mdy = 5;
  u8g2.drawBitmap(0, 0, logo_width, logo_height, makelogo_bits);
}

void drawBars(int P1, int P2, int P3, int P4) {
  u8g2.drawBox(1, 1, 10, P1);
  u8g2.drawBox(15, 1, 10, P2);
  u8g2.drawBox(30, 1, 10, P3);
  u8g2.drawBox(45, 1, 10, P4);
  //u8g.print("m/s");

}

//DRAWS THE CIRCLE ON THE SCREEN WHILE NAVIGATING
void drawBallDir(int P1, int P2, int P3, int P4) {
  int pull_x = 0;
  int pull_y = 0;
  pull_x = ((P2 - P3) / 2) + 32;
  pull_y = ((P1 - P4) / 2) + 24;
  u8g2.drawCircle(pull_x, pull_y, 4);
  ballMotorControl(pull_x, pull_y);
}

//CONTROLS THE MOTORS BASED ON THE BALL LOCATION
void ballMotorControl(int mxd, int myd) {
  int  Aspeed = 50;
  int  Bspeed = 50;
  int power = map(myd, 48, 0, 0, 100);
  int offset = map(mxd, 0, 64, 50, -50);
  Aspeed = power - offset;
  Bspeed = power + offset;
  if (Aspeed < 62 && Aspeed > 38) {
    Aspeed = 50;
  }
  if (Bspeed < 62 && Bspeed > 38) {
    Bspeed = 50;
  }
  motorA(Aspeed);
  motorB(Bspeed);

}

//DRIVES MOTOR A
void motorA(int percent) {
  int maxSpeed = 90;
  int minSpeed = 10;
  int dir = 0;
  if (percent < 50) {
    dir = 0;
  }
  if (percent > 50) {
    dir = 1;
  }
  if (dir == 1) {
    pinMode(APHASE, INPUT);
    pinMode(APWM, INPUT);
    pinMode(APHASE, OUTPUT);
    pinMode(APWM, OUTPUT);
    digitalWrite(APHASE, LOW);
    int drive = map(percent, 51, 100, 0, 255);
    drive = constrain(drive, 0, 1023);
    //SerialUSB.print("Driving Fore: ");
    //SerialUSB.println(drive);
    analogWrite(APWM, drive);
  }
  if (dir == 0) {
    pinMode(APHASE, INPUT);
    pinMode(APWM, INPUT);
    pinMode(APHASE, OUTPUT);
    pinMode(APWM, OUTPUT);
    digitalWrite(APHASE, HIGH);
    int drive = map(percent, 49, 0, 0, 255);
    drive = constrain(drive, 0, 1023);
    SerialUSB.print("Driving Back: ");
    SerialUSB.println(drive);
    analogWrite(APWM, drive);
  }
  if (percent == 50) {
    pinMode(APHASE, INPUT);
    pinMode(APWM, INPUT);
  }
}

//DRIVES MOTOR B
void motorB(int percent) {
  int maxSpeed = 85;
  int minSpeed = 45;
  int dir = 0;
  if (percent < 50) {
    dir = 0;
  }
  if (percent > 50) {
    dir = 1;
  }
  if (dir == 1) {
    pinMode(BPHASE, INPUT);
    pinMode(BPWM, INPUT);
    pinMode(BPHASE, OUTPUT);
    pinMode(BPWM, OUTPUT);
    digitalWrite(BPHASE, HIGH);
    int drive = map(percent, 51, 100, 0, 255);
    drive = constrain(drive, 0, 1023);
    SerialUSB.print("Driving Fore: ");
    SerialUSB.println(drive);
    analogWrite(BPWM, drive);
  }
  if (dir == 0) {
    pinMode(BPHASE, INPUT);
    pinMode(BPWM, INPUT);
    pinMode(BPHASE, OUTPUT);
    pinMode(BPWM, OUTPUT);
    digitalWrite(BPHASE, LOW);
    int drive = map(percent, 49, 0, 0, 255);
    drive = constrain(drive, 0, 1023);
    analogWrite(BPWM, drive);
  }
  if (percent == 50) {
    pinMode(BPHASE, INPUT);
    pinMode(BPWM, INPUT);
  }
}

//PLAYS THE INTRO MESSAGE
void intro() {
  u8g2.drawStr( 1, 10, "ANN BOT");
  u8g2.drawStr( 1, 25, "V0.1");
}


//DISPLAYS THE MENU
void menu_select() {
  menu_circle();
  u8g2.drawStr( 7, 10, "1)Simple");
  u8g2.drawStr( 7, 25, "2)TrainNN");
  u8g2.drawStr( 7, 40, "3)RunNN");
}

//DISPLAYS THE CIRCLE ON THE MENU
void menu_circle() {
  int yloc = curr_menu * 15;
  u8g2.drawCircle(3, yloc - 9, 2);
}

//LEFT BUTTON CHANGES THE MENU CIRCLE
void menu_change(void)
{
  static unsigned long last_interrupt_time = 0;
  unsigned long interrupt_time = millis();
  // If interrupts come faster than 200ms, assume it's a bounce and ignore
  if (interrupt_time - last_interrupt_time > 50)
  {
    int buttState = digitalRead(left_b);
    if (buttState == 0) {
      curr_menu++;
      if (curr_menu > menu_items) {
        curr_menu = 1;
      }
    }
  }
  last_interrupt_time = interrupt_time;
}

void load_prog() {
  prog_start = 1;
}

//TRAINS THE NEURAL NETWORK
void train_nn() {
  /******************************************************************
    Initialize HiddenWeights and ChangeHiddenWeights
  ******************************************************************/
  prog_start = 0;
  digitalWrite(LEDYEL, LOW);
  for ( i = 0 ; i < HiddenNodes ; i++ ) {
    for ( j = 0 ; j <= InputNodes ; j++ ) {
      ChangeHiddenWeights[j][i] = 0.0 ;
      Rando = float(random(100)) / 100;
      HiddenWeights[j][i] = 2.0 * ( Rando - 0.5 ) * InitialWeightMax ;
    }
  }
  digitalWrite(LEDYEL, HIGH);
  /******************************************************************
    Initialize OutputWeights and ChangeOutputWeights
  ******************************************************************/
  digitalWrite(LEDRED, LOW);
  for ( i = 0 ; i < OutputNodes ; i ++ ) {
    for ( j = 0 ; j <= HiddenNodes ; j++ ) {
      ChangeOutputWeights[j][i] = 0.0 ;
      Rando = float(random(100)) / 100;
      OutputWeights[j][i] = 2.0 * ( Rando - 0.5 ) * InitialWeightMax ;
    }
  }
  digitalWrite(LEDRED, HIGH);
  //SerialUSB.println("Initial/Untrained Outputs: ");
  //toTerminal();
  /******************************************************************
    Begin training
  ******************************************************************/

  for ( TrainingCycle = 1 ; TrainingCycle < 2147483647 ; TrainingCycle++) {

    /******************************************************************
      Randomize order of training patterns
    ******************************************************************/

    for ( p = 0 ; p < PatternCount ; p++) {
      q = random(PatternCount);
      r = RandomizedIndex[p] ;
      RandomizedIndex[p] = RandomizedIndex[q] ;
      RandomizedIndex[q] = r ;
    }
    Error = 0.0 ;
    /******************************************************************
      Cycle through each training pattern in the randomized order
    ******************************************************************/
    for ( q = 0 ; q < PatternCount ; q++ ) {
      p = RandomizedIndex[q];

      /******************************************************************
        Compute hidden layer activations
      ******************************************************************/
      digitalWrite(LEDYEL, LOW);
      for ( i = 0 ; i < HiddenNodes ; i++ ) {
        Accum = HiddenWeights[InputNodes][i] ;
        for ( j = 0 ; j < InputNodes ; j++ ) {
          Accum += Input[p][j] * HiddenWeights[j][i] ;
        }
        Hidden[i] = 1.0 / (1.0 + exp(-Accum)) ;
      }
      digitalWrite(LEDYEL, HIGH);

      /******************************************************************
        Compute output layer activations and calculate errors
      ******************************************************************/
      digitalWrite(LEDRED, LOW);
      for ( i = 0 ; i < OutputNodes ; i++ ) {
        Accum = OutputWeights[HiddenNodes][i] ;
        for ( j = 0 ; j < HiddenNodes ; j++ ) {
          Accum += Hidden[j] * OutputWeights[j][i] ;
        }
        Output[i] = 1.0 / (1.0 + exp(-Accum)) ;
        OutputDelta[i] = (Target[p][i] - Output[i]) * Output[i] * (1.0 - Output[i]) ;
        Error += 0.5 * (Target[p][i] - Output[i]) * (Target[p][i] - Output[i]) ;
      }
      //SerialUSB.println(Output[0]*100);
      digitalWrite(LEDRED, HIGH);
      /******************************************************************
        Backpropagate errors to hidden layer
      ******************************************************************/
      digitalWrite(LEDYEL, LOW);
      for ( i = 0 ; i < HiddenNodes ; i++ ) {
        Accum = 0.0 ;
        for ( j = 0 ; j < OutputNodes ; j++ ) {
          Accum += OutputWeights[i][j] * OutputDelta[j] ;
        }
        HiddenDelta[i] = Accum * Hidden[i] * (1.0 - Hidden[i]) ;
      }
      digitalWrite(LEDYEL, HIGH);

      /******************************************************************
        Update Inner-->Hidden Weights
      ******************************************************************/

      digitalWrite(LEDRED, LOW);
      for ( i = 0 ; i < HiddenNodes ; i++ ) {
        ChangeHiddenWeights[InputNodes][i] = LearningRate * HiddenDelta[i] + Momentum * ChangeHiddenWeights[InputNodes][i] ;
        HiddenWeights[InputNodes][i] += ChangeHiddenWeights[InputNodes][i] ;
        for ( j = 0 ; j < InputNodes ; j++ ) {
          ChangeHiddenWeights[j][i] = LearningRate * Input[p][j] * HiddenDelta[i] + Momentum * ChangeHiddenWeights[j][i];
          HiddenWeights[j][i] += ChangeHiddenWeights[j][i] ;
        }
      }
      digitalWrite(LEDRED, HIGH);
      /******************************************************************
        Update Hidden-->Output Weights
      ******************************************************************/
      digitalWrite(LEDYEL, LOW);
      for ( i = 0 ; i < OutputNodes ; i ++ ) {
        ChangeOutputWeights[HiddenNodes][i] = LearningRate * OutputDelta[i] + Momentum * ChangeOutputWeights[HiddenNodes][i] ;
        OutputWeights[HiddenNodes][i] += ChangeOutputWeights[HiddenNodes][i] ;
        for ( j = 0 ; j < HiddenNodes ; j++ ) {
          ChangeOutputWeights[j][i] = LearningRate * Hidden[j] * OutputDelta[i] + Momentum * ChangeOutputWeights[j][i] ;
          OutputWeights[j][i] += ChangeOutputWeights[j][i] ;
        }
      }
      digitalWrite(LEDYEL, HIGH);
    }

    /******************************************************************
      Every 100 cycles send data to terminal for display and draws the graph on OLED
    ******************************************************************/
    ReportEvery1000 = ReportEvery1000 - 1;
    if (ReportEvery1000 == 0)
    {
      int graphNum = TrainingCycle / 100;
      int graphE1 = Error * 1000;
      int graphE = map(graphE1, 3, 80, 47, 0);
      ErrorGraph[graphNum] = graphE;
      u8g2.firstPage();
      do {
        drawGraph();
      } while ( u8g2.nextPage() );

      SerialUSB.println();
      SerialUSB.println();
      SerialUSB.print ("TrainingCycle: ");
      SerialUSB.print (TrainingCycle);
      SerialUSB.print ("  Error = ");
      SerialUSB.println (Error, 5);
      SerialUSB.print ("  Graph Num: ");
      SerialUSB.print (graphNum);
      SerialUSB.print ("  Graph Error1 = ");
      SerialUSB.print (graphE1);
      SerialUSB.print ("  Graph Error = ");
      SerialUSB.println (graphE);

      toTerminal();

      if (TrainingCycle == 1)
      {
        ReportEvery1000 = 99;
      }
      else
      {
        ReportEvery1000 = 100;
      }
    }


    /******************************************************************
      If error rate is less than pre-determined threshold then end
    ******************************************************************/

    if ( Error < Success ) break ;
  }
}

//USES TRAINED NEURAL NETWORK TO DRIVE ROBOT
void drive_nn()
{
  SerialUSB.println("Running NN Drive Test");
  if (Success < Error) {
    prog_start = 0;
    SerialUSB.println("NN not Trained");
  }
  while (Error < Success) {
    int num;
    int farDist = 35;
    int closeDist = 7;
    float TestInput[] = {0, 0, 0, 0};
    digitalWrite(LEDYEL, LOW);

    int LL1 = analogRead(A1);   // Collect sonar distances.
    int LL2 = analogRead(A2);   // Collect sonar distances.
    int LL3 = analogRead(A3);   // Collect sonar distances.
    int LL4 = analogRead(A4);   // Collect sonar distances.

#ifdef DEBUG
    SerialUSB.print("Light Level: ");
    SerialUSB.print(LL1);
    SerialUSB.print("\t");
    SerialUSB.print(LL2);
    SerialUSB.print("\t");
    SerialUSB.print(LL3);
    SerialUSB.print("\t");
    SerialUSB.println(LL4);
#endif

    digitalWrite(LEDYEL, HIGH);

    LL1 = map(LL1, 400, 1024, 0, 100);
    LL2 = map(LL2, 400, 1024, 0, 100);
    LL3 = map(LL3, 400, 1024, 0, 100);
    LL4 = map(LL4, 400, 1024, 0, 100);

    LL1 = constrain(LL1, 0, 100);
    LL2 = constrain(LL2, 0, 100);
    LL3 = constrain(LL3, 0, 100);
    LL4 = constrain(LL4, 0, 100);

    TestInput[0] = float(LL1) / 100;
    TestInput[1] = float(LL2) / 100;
    TestInput[2] = float(LL3) / 100;
    TestInput[3] = float(LL4) / 100;
#ifdef DEBUG
    SerialUSB.print("Input: ");
    SerialUSB.print(TestInput[3], 2);
    SerialUSB.print("\t");
    SerialUSB.print(TestInput[2], 2);
    SerialUSB.print("\t");
    SerialUSB.print(TestInput[1], 2);
    SerialUSB.print("\t");
    SerialUSB.println(TestInput[0], 2);
#endif

    InputToOutput(TestInput[0], TestInput[1], TestInput[2], TestInput[3]); //INPUT to ANN to obtain OUTPUT

    int speedA = Output[0] * 100;
    int speedB = Output[1] * 100;
    speedA = int(speedA);
    speedB = int(speedB);
#ifdef DEBUG
    SerialUSB.print("Speed: ");
    SerialUSB.print(speedA);
    SerialUSB.print("\t");
    SerialUSB.println(speedB);
#endif
    motorA(speedA);
    motorB(speedB);
    delay(50);
  }
}

void drawGraph() {
  for (int x = 2; x < 64; x++) {
    u8g2.drawLine(x - 1, ErrorGraph[x - 2], x - 1, ErrorGraph[x - 1]);
  }
}

//DISPLAYS INFORMATION WHILE TRAINING
void toTerminal()
{

  for ( p = 0 ; p < PatternCount ; p++ ) {
    SerialUSB.println();
    SerialUSB.print ("  Training Pattern: ");
    SerialUSB.println (p);
    SerialUSB.print ("  Input ");
    for ( i = 0 ; i < InputNodes ; i++ ) {
      SerialUSB.print (Input[p][i], DEC);
      SerialUSB.print (" ");
    }
    SerialUSB.print ("  Target ");
    for ( i = 0 ; i < OutputNodes ; i++ ) {
      SerialUSB.print (Target[p][i], DEC);
      SerialUSB.print (" ");
    }
    /******************************************************************
      Compute hidden layer activations
    ******************************************************************/

    for ( i = 0 ; i < HiddenNodes ; i++ ) {
      Accum = HiddenWeights[InputNodes][i] ;
      for ( j = 0 ; j < InputNodes ; j++ ) {
        Accum += Input[p][j] * HiddenWeights[j][i] ;


      }
      Hidden[i] = 1.0 / (1.0 + exp(-Accum)) ;
    }

    /******************************************************************
      Compute output layer activations and calculate errors
    ******************************************************************/

    for ( i = 0 ; i < OutputNodes ; i++ ) {
      Accum = OutputWeights[HiddenNodes][i] ;
      for ( j = 0 ; j < HiddenNodes ; j++ ) {
        Accum += Hidden[j] * OutputWeights[j][i] ;
      }
      Output[i] = 1.0 / (1.0 + exp(-Accum)) ;
    }
    //SerialUSB.print ("  Output ");
    //for ( i = 0 ; i < OutputNodes ; i++ ) {
    //  SerialUSB.print (Output[i], 5);
    //  SerialUSB.print (" ");
    // }
  }
}

void InputToOutput(float In1, float In2, float In3, float In4)
{
  float TestInput[] = {0, 0, 0, 0};
  TestInput[0] = In1;
  TestInput[1] = In2;
  TestInput[2] = In3;
  TestInput[3] = In4;

  /******************************************************************
    Compute hidden layer activations
  ******************************************************************/

  for ( i = 0 ; i < HiddenNodes ; i++ ) {
    Accum = HiddenWeights[InputNodes][i] ;
    for ( j = 0 ; j < InputNodes ; j++ ) {
      Accum += TestInput[j] * HiddenWeights[j][i] ;
    }
    Hidden[i] = 1.0 / (1.0 + exp(-Accum)) ;
  }

  /******************************************************************
    Compute output layer activations and calculate errors
  ******************************************************************/

  for ( i = 0 ; i < OutputNodes ; i++ ) {
    Accum = OutputWeights[HiddenNodes][i] ;
    for ( j = 0 ; j < HiddenNodes ; j++ ) {
      Accum += Hidden[j] * OutputWeights[j][i] ;
    }
    Output[i] = 1.0 / (1.0 + exp(-Accum)) ;
  }
#ifdef DEBUG
  SerialUSB.print ("  Output ");
  for ( i = 0 ; i < OutputNodes ; i++ ) {
    SerialUSB.print (Output[i], 5);
    SerialUSB.print (" ");
  }
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

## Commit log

2017-10-29 added firmware
    [make_nn_bot.kicad_pcb]
2017-10-31 Bootloader added
    [make_nn_bot.kicad_pcb]
2017-11-06 updated gerbs
    [make_nn_bot-B.Cu.gbr, make_nn_bot-B.Mask.gbr, make_nn_bot-B.SilkS.gbr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]
2017-11-06 not needed file
    [LaserLayout.dxf]
2017-11-16 corrected some components
    [BOM.csv]
2018-05-12 small revisions
    [make_nn_bot.csv, make_nn_bot.sch]
